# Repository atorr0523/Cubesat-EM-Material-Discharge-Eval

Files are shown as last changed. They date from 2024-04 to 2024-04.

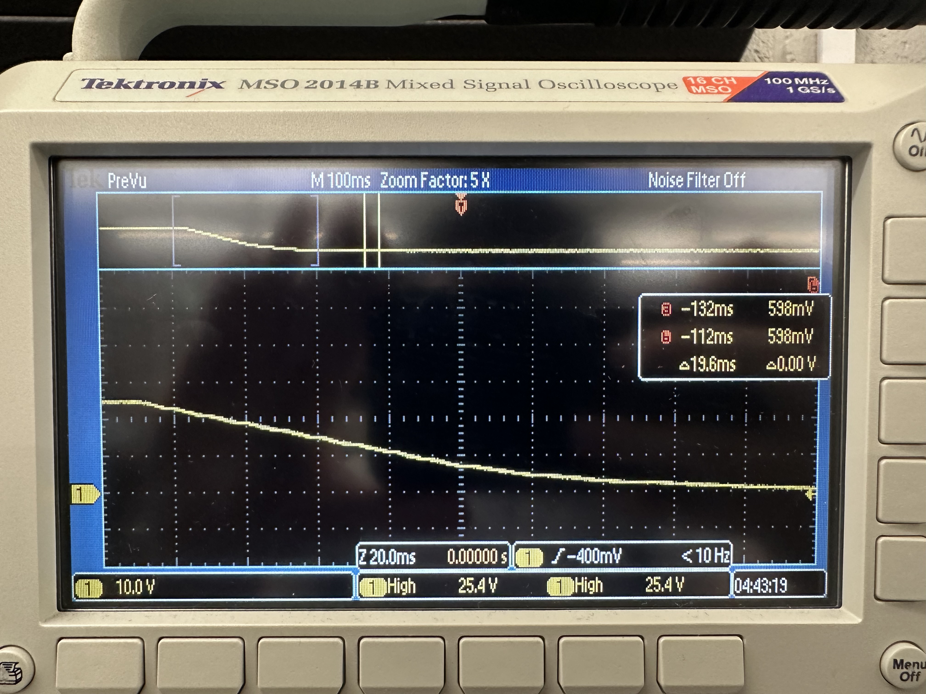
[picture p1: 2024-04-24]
ChassisandModeling/LVTesting/IMG_3064.jpg

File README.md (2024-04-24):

# CubeSat-EM-Material-Discharge-Eval
ECEN 403 904 Capstone Team 44 

For this project, we are tasked to design and develop the first prototype of Orbital Arc's RIOT Drive or CubeSat.

We divided it into 4 separate subsystems and at the end integrated each subsystem accordingly.

The Chassis and Modeling subsystem is designed to hold the integrated PCB as well as the accelerator plates that are designed.

The accelerator modeling subsystem helps with the design of the accelerator plate that would be mounted onto the CubeSat.
Simulations were performed amongst 3 different geometries and 3 different materials in order to see which iteration of 
the plate would fit well within the CubeSat's standards. 

The microcontroller subsystem, which is powered from the power PCB, helps control the system as well as the stepper motor controller which is used
for a gas feed valve.

The power circuit subsystem takes the input voltage and converts the voltage to power the components within the system.

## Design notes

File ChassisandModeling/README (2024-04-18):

My Chassis and Modeling folder contains the work performed for creation of the Chassis and Mounting, as well as other tasks completed by me

In this Chassis Files Folder, one will find the Solidworks and .stl files for the componenets created for this project.
In the LVTesting Folder, one will find the results from the low voltage testing performed at the beginning of the Spring 24 semester.
In the MISC. Folder, one will find hand-drawn engineering drawings or calculations in order to provide a path to continuation for interested parties.

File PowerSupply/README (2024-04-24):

For the Power Supply subsystem you will find the altium files before integrating with the microcontroller. 

The final design included the following:
  -A boost converter which steps up the voltage from 24V to 48V with a 0.62A output current needed.
  -A buck converter which steps down the voltage from 24V to 5V with a maximum output current of 2A needed for the thermionic cathodes.
  -A buck converter which steps down the voltage from 24V to 5V with a maximum output current of 1A needed for the stepper motor controller
  -A buck converter which steps down the voltage from 24V to 3.3V with a maximum output current of 1A needed to power the microcontroller.

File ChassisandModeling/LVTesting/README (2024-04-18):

This folder holds the data collected and Oscilloscope screenshots from the low voltage testing performed for Orbital Arc.
This testing was performed in order to provide Orbital Arc preliminary data of how the voltage applied to the accelerator plate will dissipate and how often it will need to be pulsed
The conclusion of this testing was that the dissipation over the intended operating range (First 10% of discharge) would be linear, and further high voltage testing would be required to get the actual dissipation curve
At this point, further testing was not able to take place and neglected, with my priority shifting to physical integration of the prototype

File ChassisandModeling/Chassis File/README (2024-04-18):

This folder contains all of the design files for the Chassis and Mounting Devices created. 
It also contains the files for the connector to the gas feed valve and DC Motor
This folder contains Solidworks files, Solidworks drawings, and .STL files

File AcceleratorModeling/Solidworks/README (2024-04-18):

These files are created in the Solidworks software. They are created for the nine geometry-material prototypes and to be tested with. There is another file for the chosen prototype with designed mounting. 
The Circular Plates are fabricated by hand so there are no Solidworks files for them.

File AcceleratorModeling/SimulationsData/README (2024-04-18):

These are files that contain the simulations from the ANSYS Maxwell software. These are created to simulate the electric field for each prototype after charging with 100kV. There is also an spreadsheet that contains the data that I have collected.

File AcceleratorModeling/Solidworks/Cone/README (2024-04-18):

These are files for the cone-shaped prototypes

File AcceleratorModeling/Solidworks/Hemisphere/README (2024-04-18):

These are files for the hemisphere-shaped prototypes

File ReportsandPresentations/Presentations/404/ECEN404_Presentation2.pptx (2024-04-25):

## ECEN 404 Team #44 Biweekly Update 2 Cubesat EM Material Discharge Eval: Ian Poynter Joshua Feldman Michael Kim Alejandro Torres Sponsor: Orbital Arc & SATOP TA: Souryendu Das

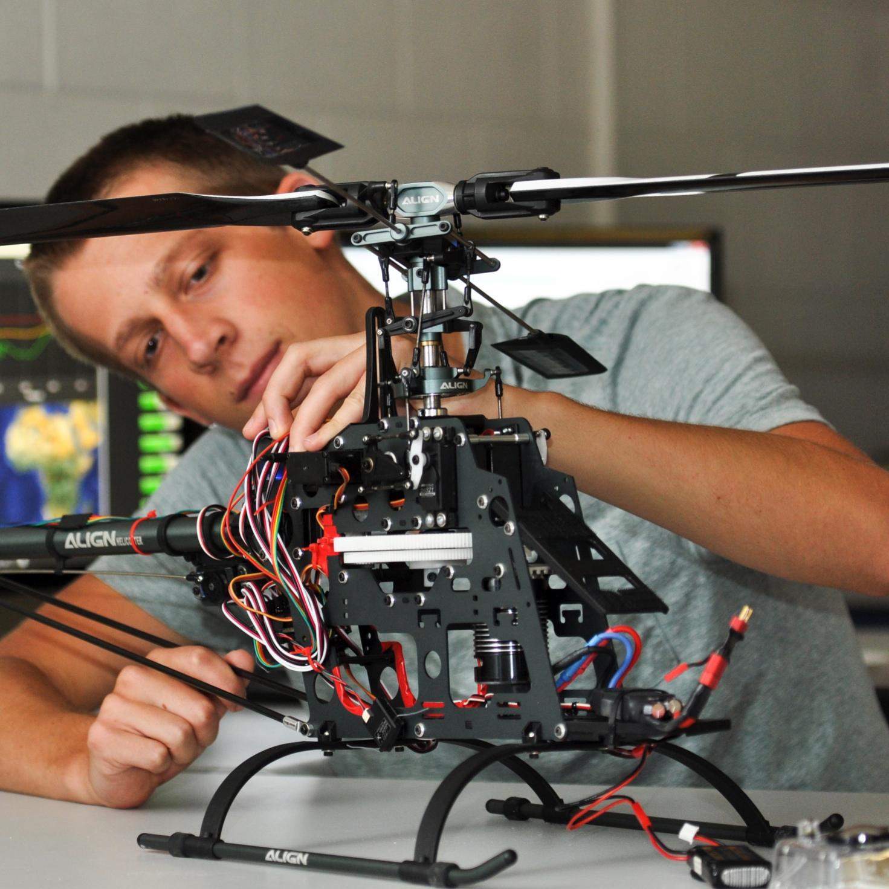
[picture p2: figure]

## Project Summary

- Develop the first prototype for the RIOT Drive
  - Interior Electronics
  - Gas Feed Control
  - Component Selection for Accelerator Plate

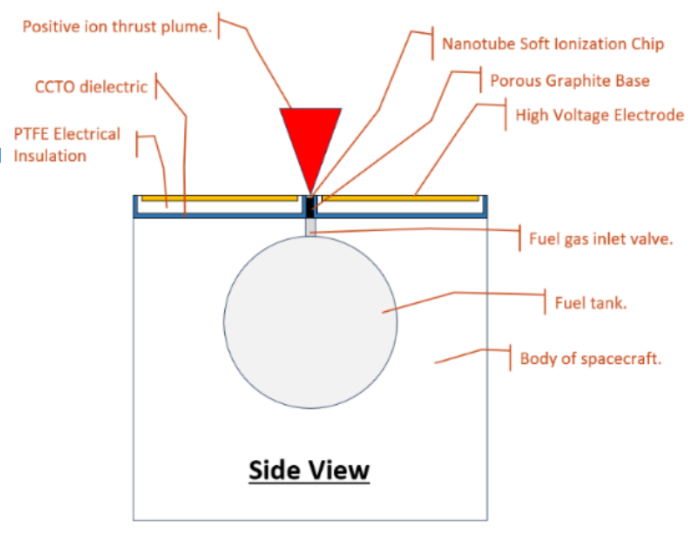
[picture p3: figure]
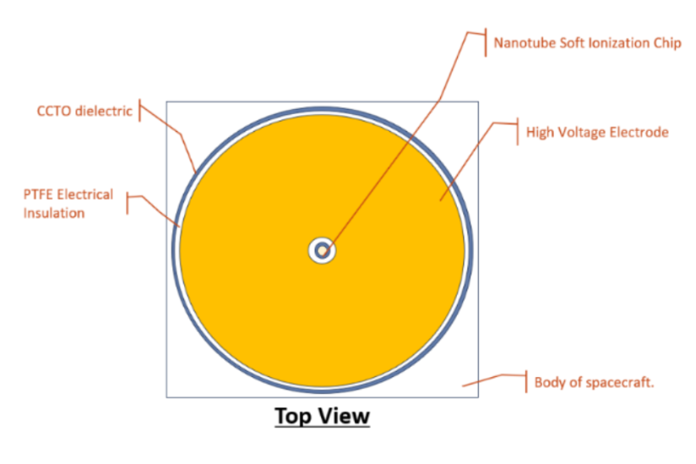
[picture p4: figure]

## Diagram of Subsystems

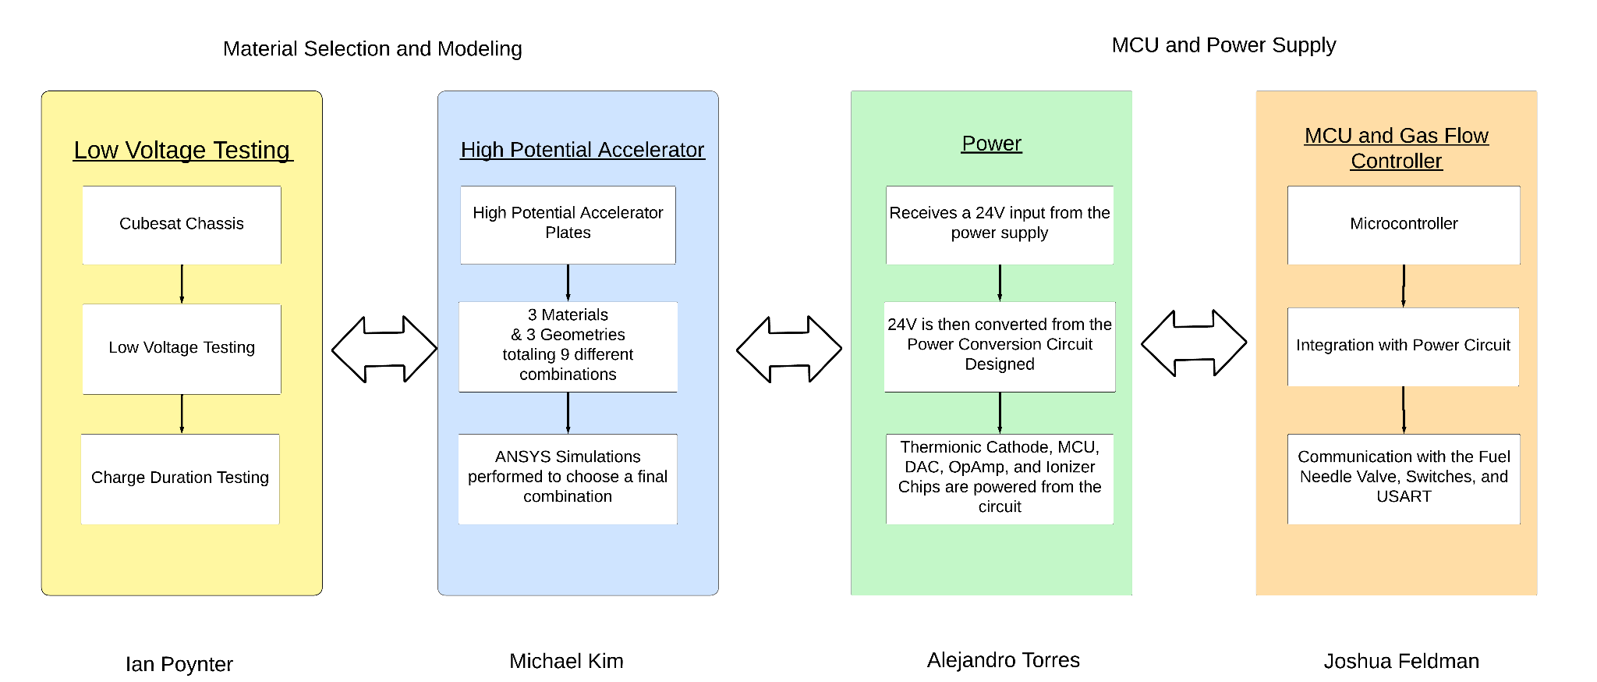
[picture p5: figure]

## Project Timeline

Mechanical Subsystems Design and Testing (completed 12/3) | Hardware Subsystems Redesign and Testing (to complete by 2/22) | Integration of Microcontroller and Power Subsystems (to complete by 3/18) | Validation of Integrated Hardware (to complete by 3/28) | Component Selection for Accelerator Plate (to complete by 3/28) | Final Integration (to complete by 4/12) | Final Demo (to complete by 4/19)

## Power Subsystem Alejandro Torres

Accomplishments since Presentation 1 18 hrs of effort | Ongoing progress/problems and plans until the next presentation
Completed Altium Schematic and PCB Layout configured and routed for integration with Microcontroller PCB and parts ordered to test in preparation for integration | Solder PCB and test through E-Load in preparation for integration with Microcontroller

## Microcontroller Joshua Feldman

Accomplishments since Presentation 1 20 hrs of effort | Ongoing progress/problems and plans until the next presentation
Reworked microcontroller board for changed inputs, for easier programming, and for future integration with power PCB. Ordered parts for PCB. MCU coded and tested for sending user inputs and control bits to DAC through SPI. | Order Fuel Valve Rework and order PCB for stepper motor control. Continue working with Alejandro for PCB integration.

## Low Voltage Physical Testing Ian Poynter

Accomplishments since Presentation 1 18 hrs of effort | Ongoing progress/problems and plans until the next presentation
Developed low voltage test setup and procedure Ordered parts for testing | Construct testing setup on breadboard Perform trial tests and validate data with sponsor

## High Potential Accelerator Plate Michael Kim

Accomplishments since Presentation 1 16 hrs of effort | Ongoing progress/problems and plans until the next presentation
Completed high-voltage simulations of circular plate geometry on Ansys Maxwell software. | Complete high-voltage simulations for hemisphere geometry. Start high-voltage simulations for cone geometry.

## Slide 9

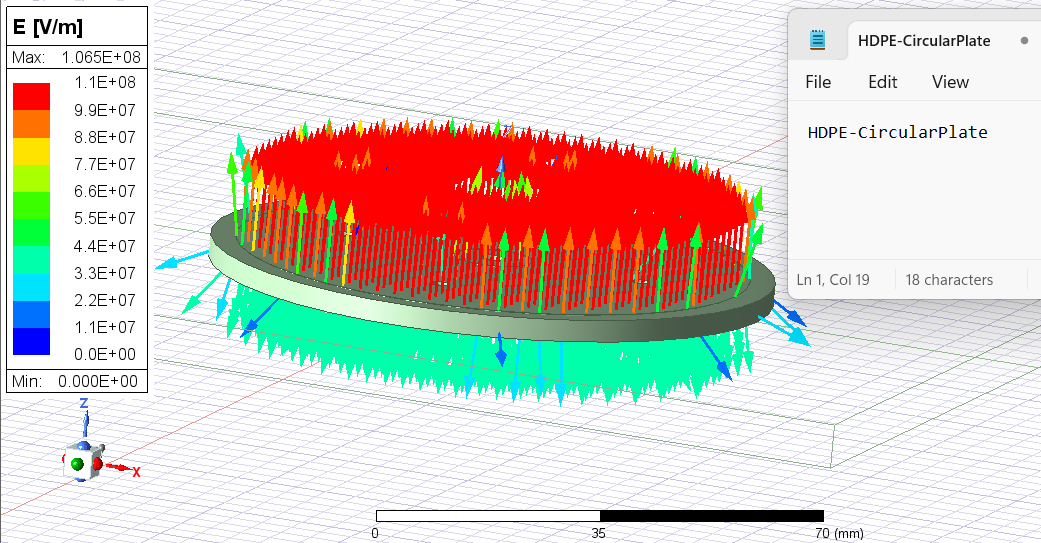
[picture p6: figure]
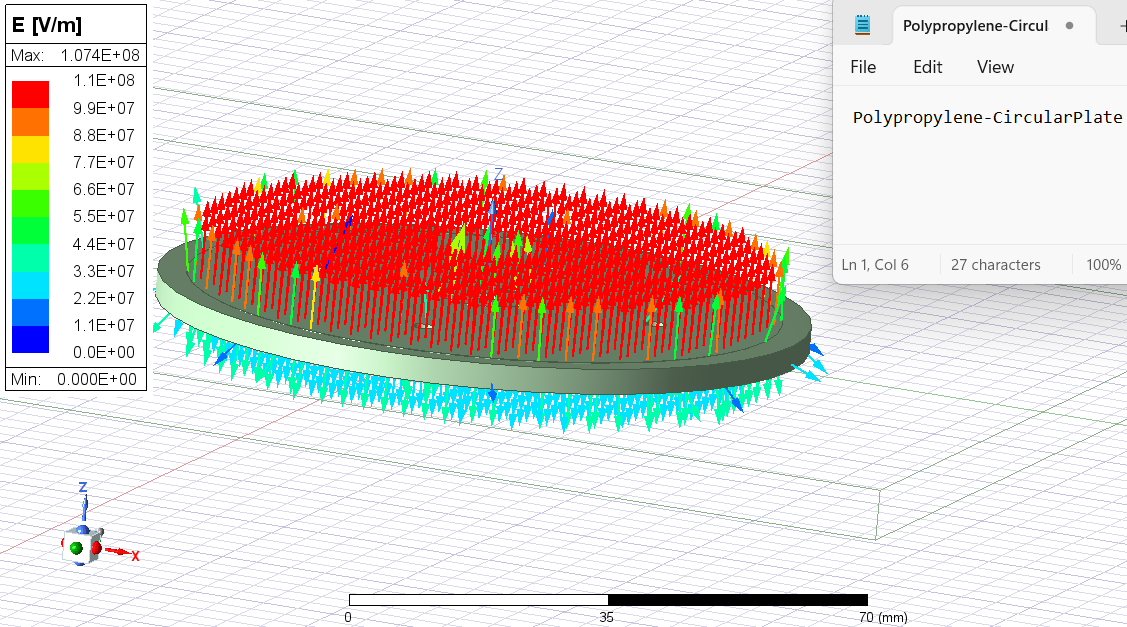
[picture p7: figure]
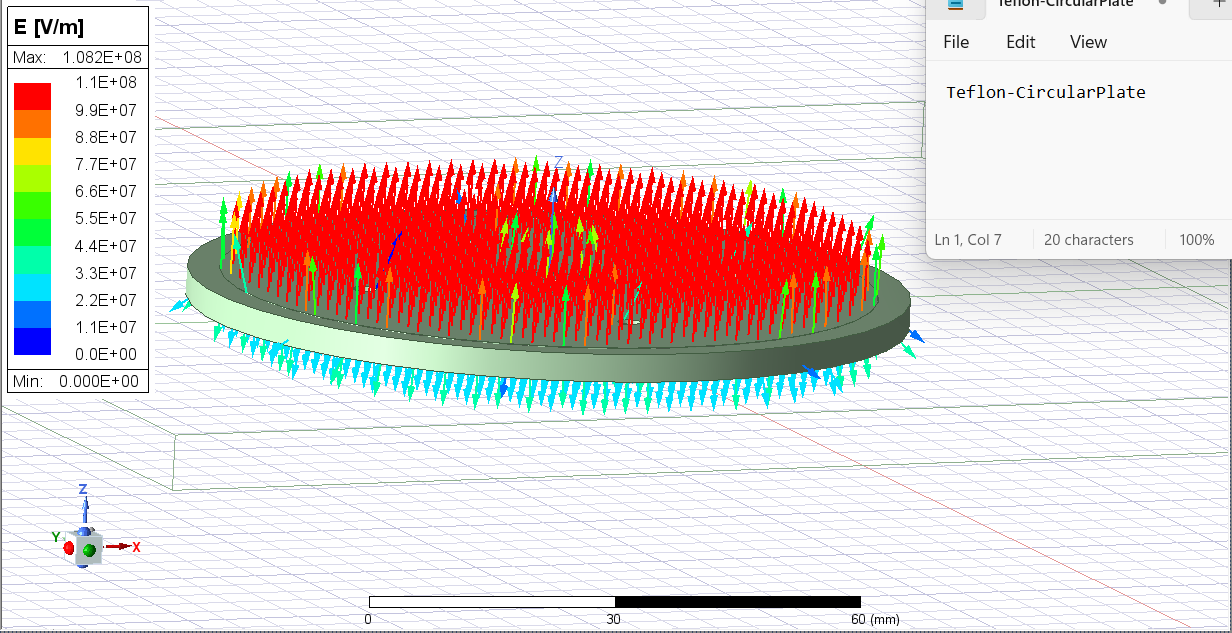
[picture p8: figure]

## Execution Plan

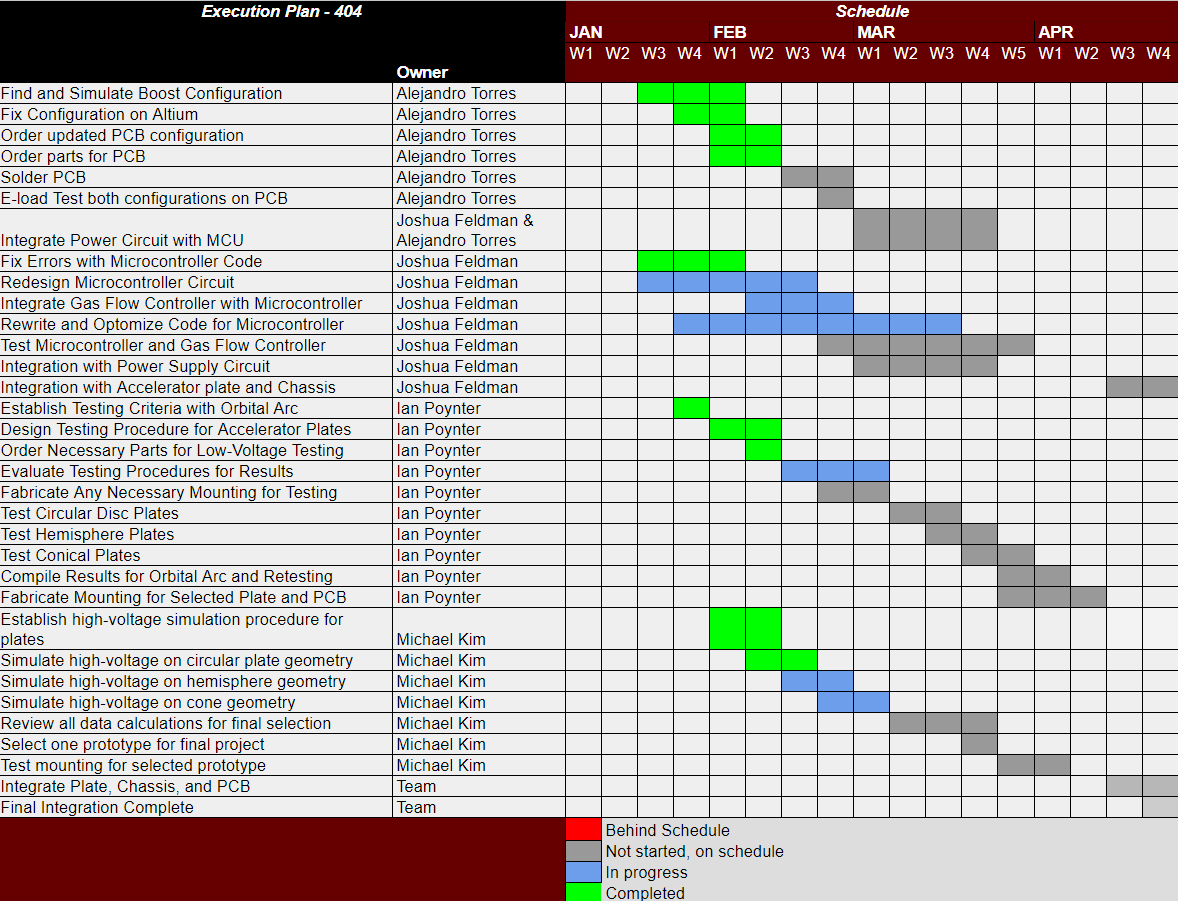
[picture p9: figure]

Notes: Michelle

## Validation Plan

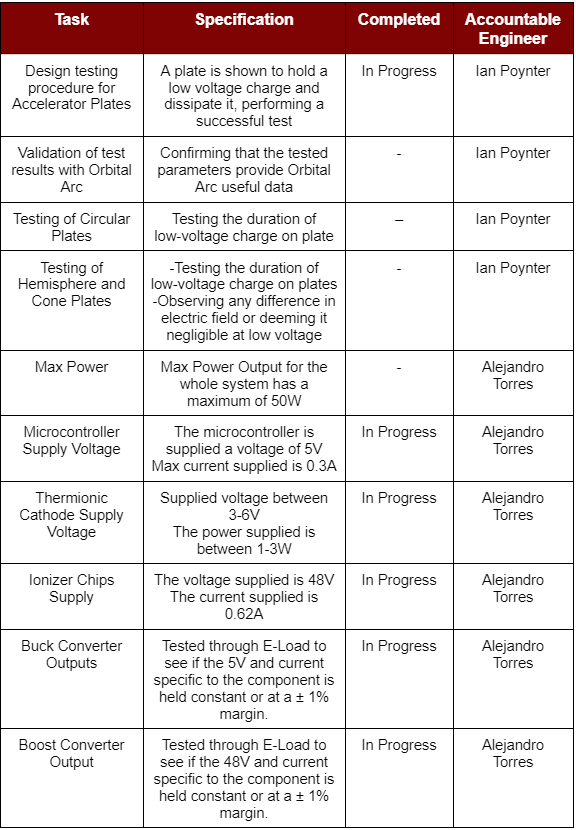
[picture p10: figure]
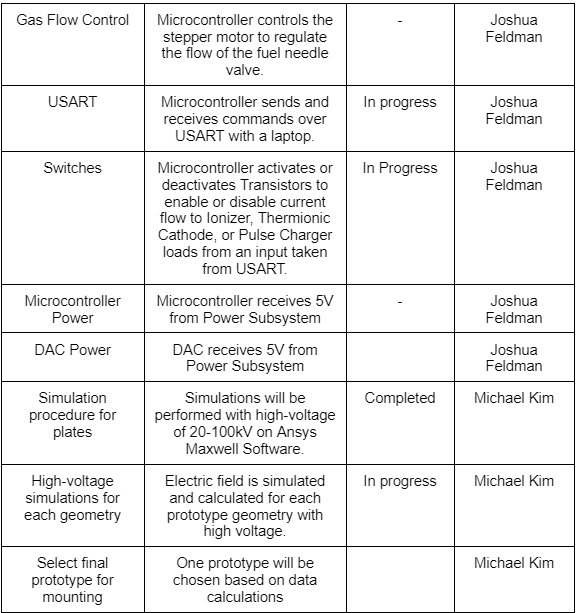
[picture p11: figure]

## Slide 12

Thank you!

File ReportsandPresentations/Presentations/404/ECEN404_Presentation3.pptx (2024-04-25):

## ECEN 404 Team #44 Biweekly Update 3 Cubesat EM Material Discharge Eval: Ian Poynter Joshua Feldman Michael Kim Alejandro Torres Sponsor: Orbital Arc & SATOP TA: Souryendu Das

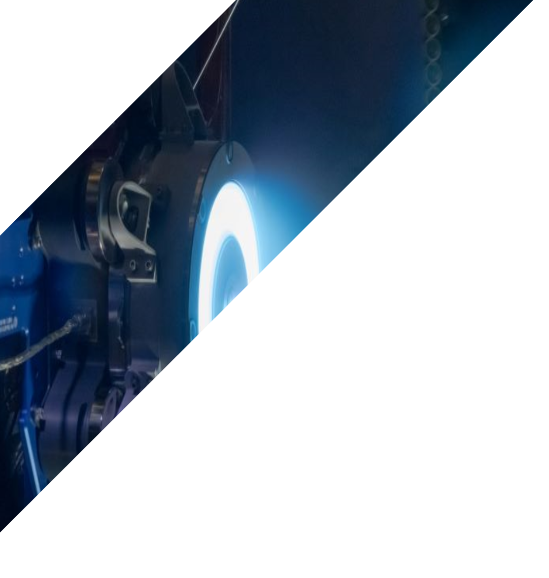
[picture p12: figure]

## Problem Statement

Current Ion Thrusters have limited use cases due to many factors, including fuel cost and harsh ionization methods

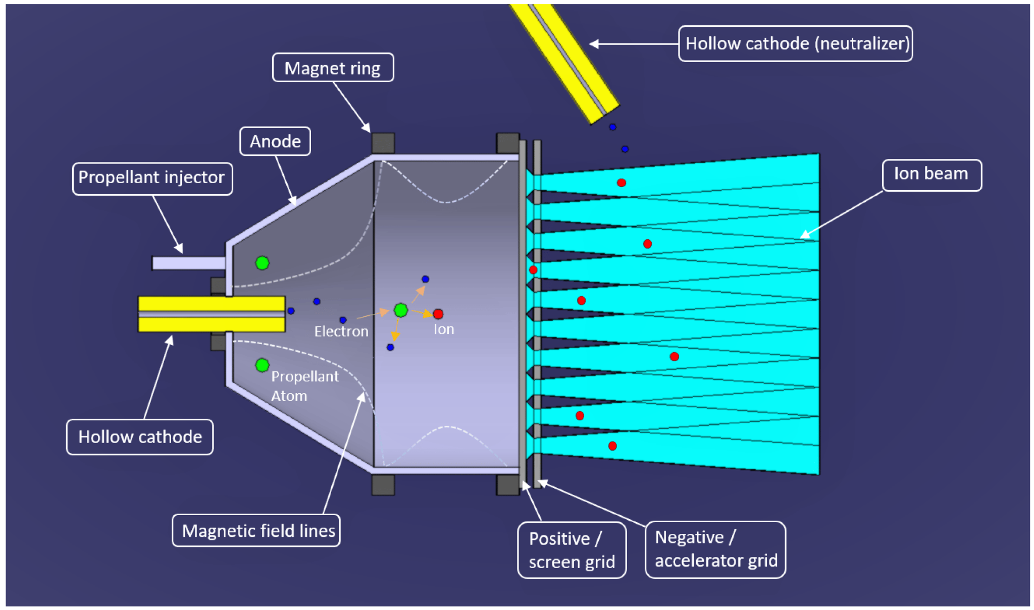
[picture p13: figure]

## Project Summary

RIOT Drive: New type of Ion Thruster that will reduce these limitations and operate with higher efficiency
Solution
- Develop a prototype for the RIOT Drive
  - Internal Hardware
    - Power Supply
    - Microcontroller
  - Accelerator Plate
    - Geometry Selection


## Diagram of Subsystems


## Project Timeline

Mechanical Subsystems Design and Testing (completed 12/3) | Hardware Subsystems Redesign and Testing (to complete by 2/22) | Integration of Microcontroller and Power Subsystems (to complete by 3/18) | Validation of Integrated Hardware (to complete by 3/28) | Component Selection for Accelerator Plate (to complete by 3/28) | Final Integration (to complete by 4/12) | Final Demo (to complete by 4/19)

## Power Subsystem Alejandro Torres

Accomplishments since last update 16 hrs of effort | Ongoing progress/problems and plans until the next presentation
Boost Converter soldered and E-load tested. | Fix Boost Converter maximum load current. Solder and test the rest of the PCB. Configure Altium Schematic for Buck converter to power the stepper motor drive.

## Power Subsystem Alejandro Torres

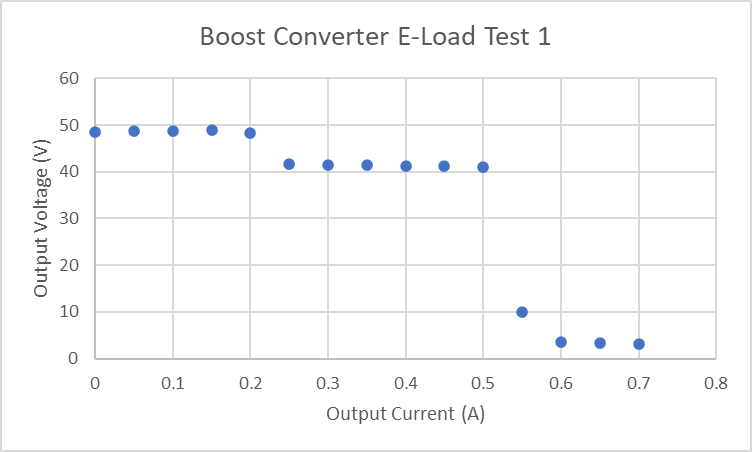
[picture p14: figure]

- Boost Converter Tested through Electronic Load.
- 48V was not kept constant throughout varying load currents in Test 1 and Test 2.
- Need to configure PCB to fix this issue.

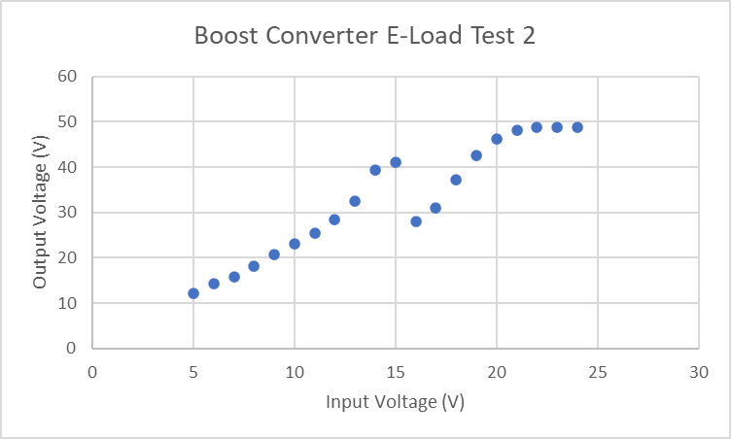
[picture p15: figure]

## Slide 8

Microcontroller
Joshua Feldman

Accomplishments since last update 12 hours of effort | Ongoing progress/problems and plans until the next presentation
Re-coded microcontroller for sponsor’s change to gas flow valve and stepper motor. Changed PCB to send inputs to stepper motor driver and removed now obsolete parts. Ordered board and parts for new revision. | Solder PCB after presentation. Test board with Stepper motor driver, and add stepper motor driver to PCB. Test powering microcontroller with Alejandro’s power PCB after testing board in lab and during Blitz.

## Low Voltage Physical Testing Ian Poynter

Accomplishments since last update 10 hrs of effort | Ongoing progress/problems and plans until the next presentation
Performed initial low-voltage discharge testing Reviewed data with sponsor | Work with Michael to make accelerator plate selection Begin mounting design

## High Potential Accelerator Plate Michael Kim

Accomplishments since last update 20 hrs of effort | Ongoing progress/problems and plans until the next presentation
Completed simulations for hemisphere and cone geometries. | Compare simulations using Gauss’s Law Work with Ian to select final prototype based on reviewed data.

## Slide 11

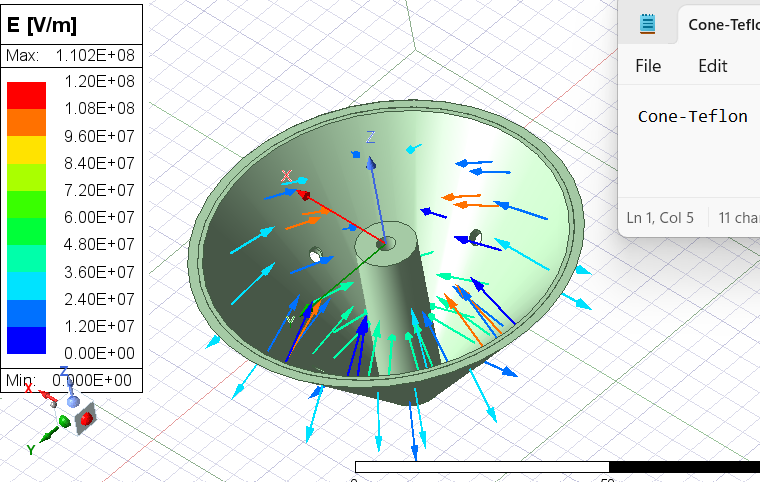
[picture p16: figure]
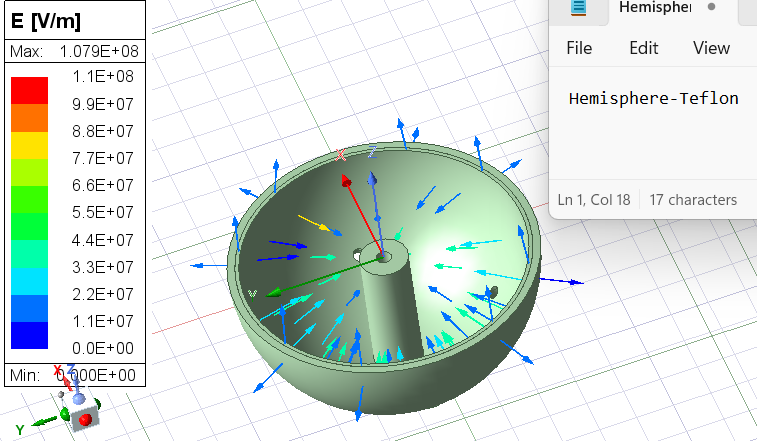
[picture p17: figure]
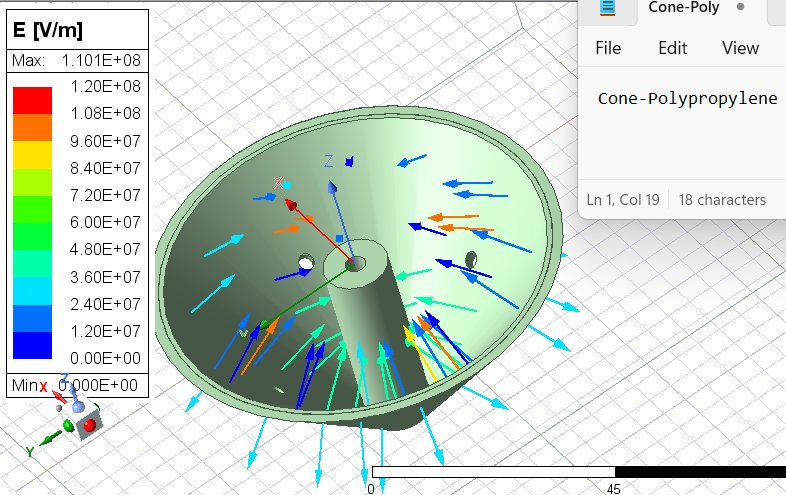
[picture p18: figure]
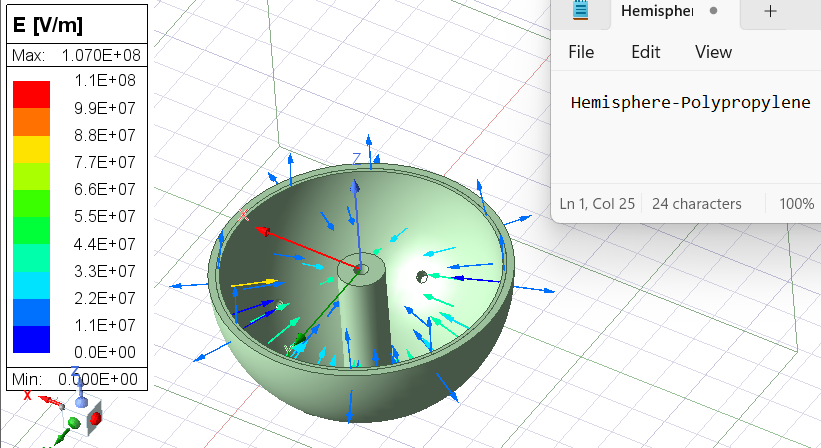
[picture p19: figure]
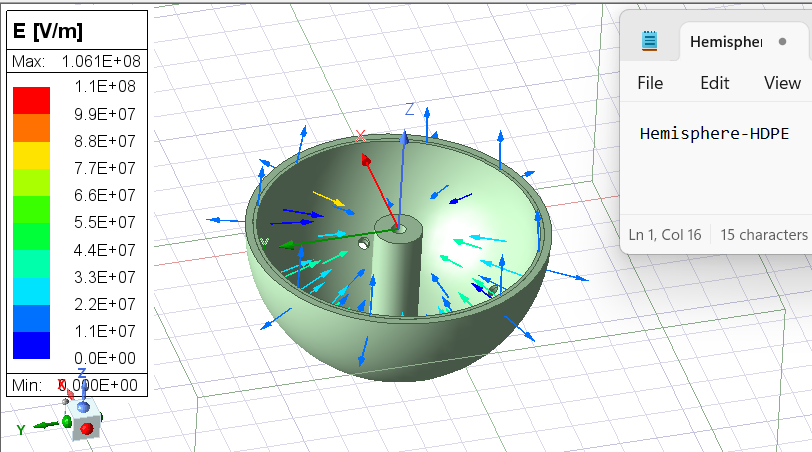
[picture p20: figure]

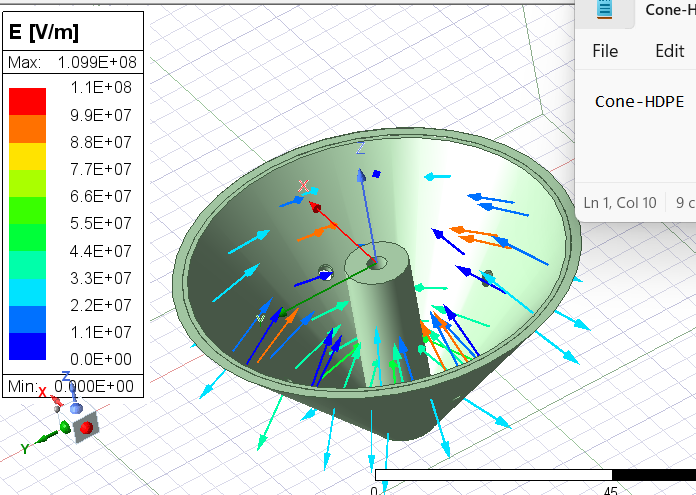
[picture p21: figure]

## Execution Plan

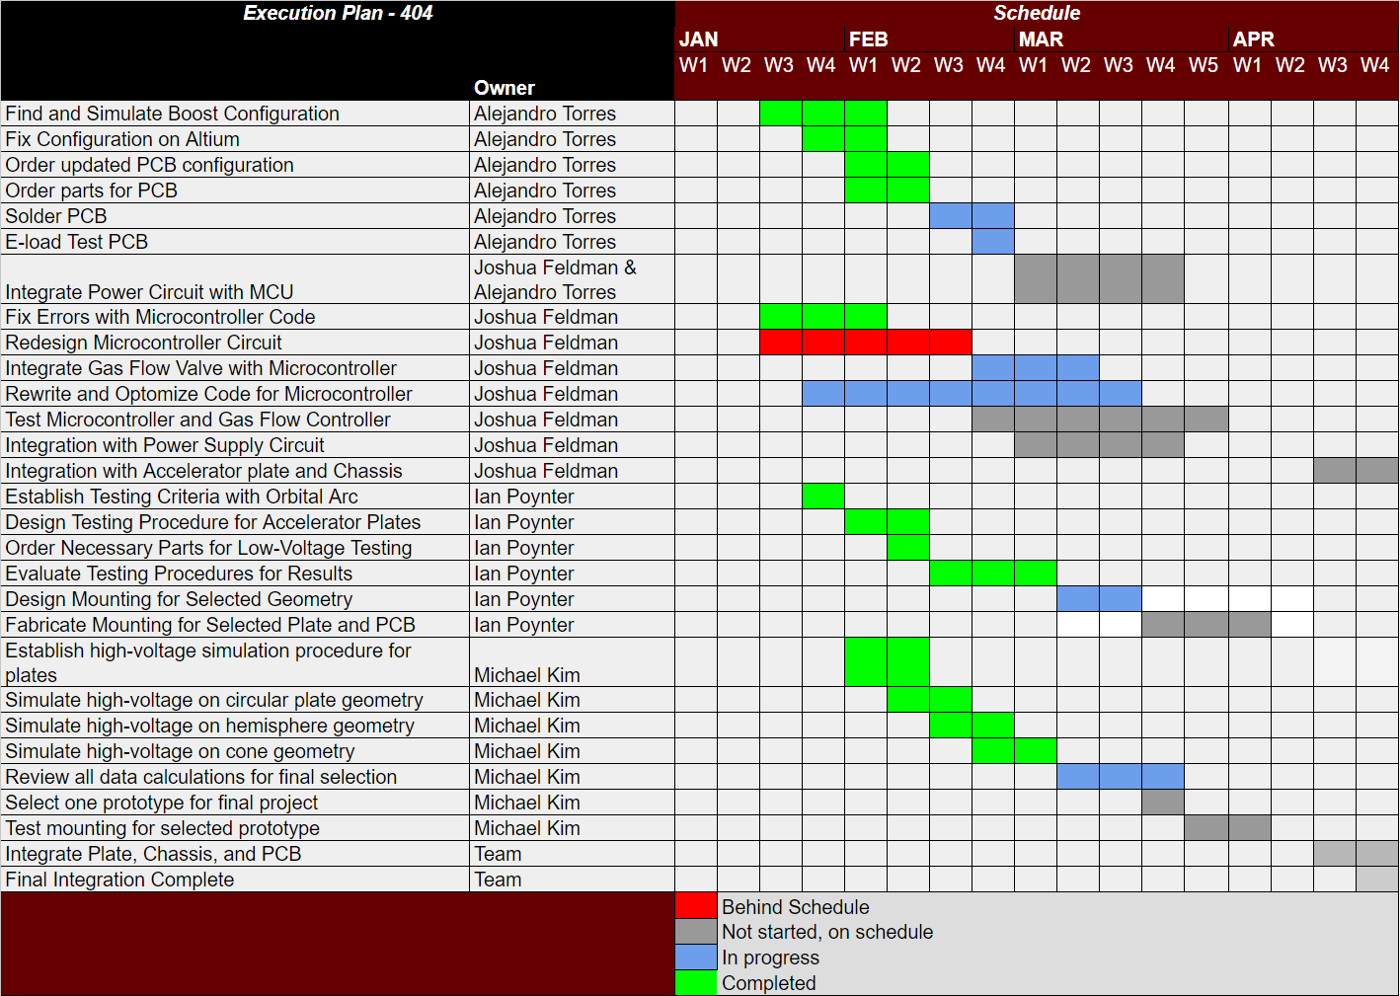
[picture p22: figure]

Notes: Michelle

## Validation Plan

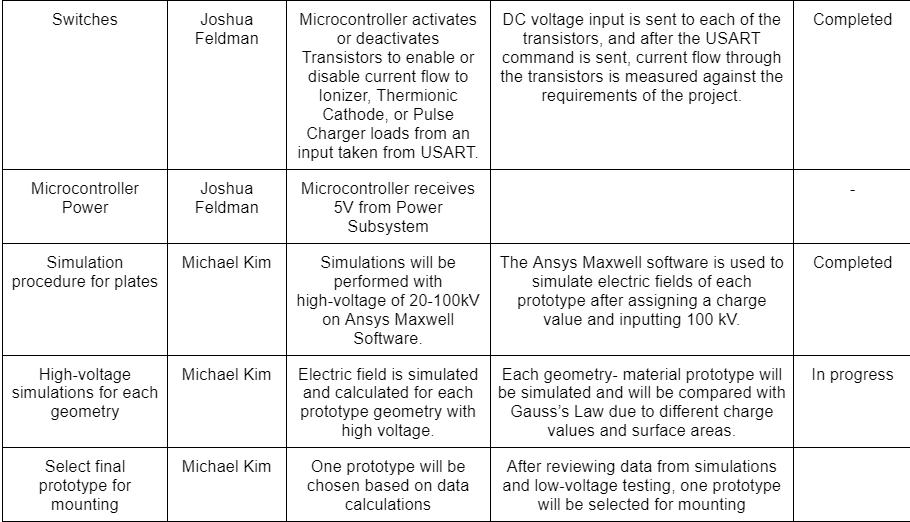
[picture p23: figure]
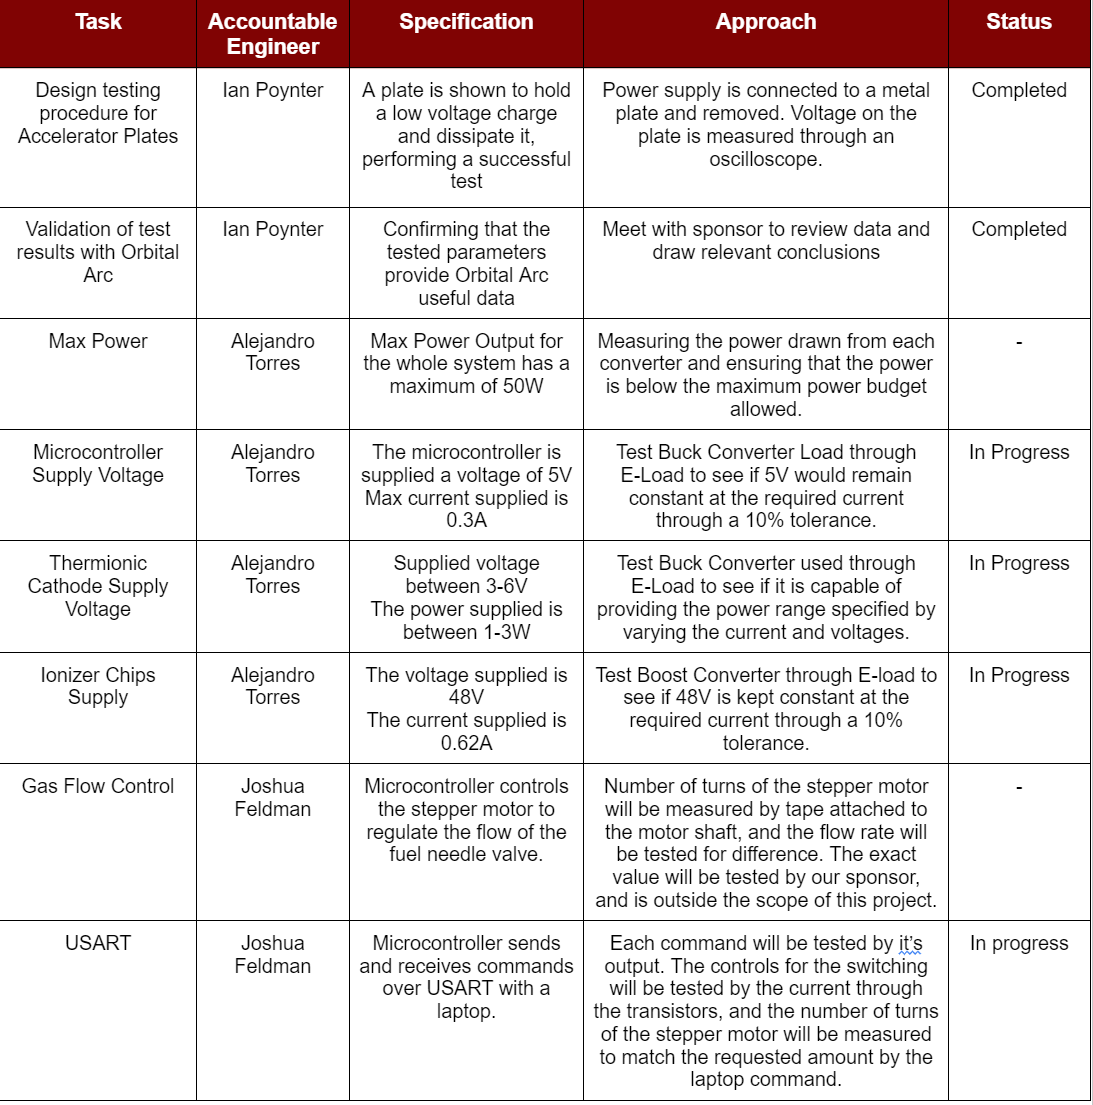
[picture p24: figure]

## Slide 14

Thank you!

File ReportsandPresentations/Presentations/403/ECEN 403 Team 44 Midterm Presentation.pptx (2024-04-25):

## ECEN 403 Team #44 Cubesat EM Material Discharge Eval: Joshua Feldman Michael Kim Ian Poynter Alejandro Torres Sponsor: Orbital Arc & SATOP TA: Peng-Hao Huang


## Current Ion Thrusters

- Current ion thrusters require expensive fuel, have extremely low acceleration, and require electron bombardment for ionization.


## RIOT Drive


- Develop a prototype for the RIOT Drive, an ion thruster that can use cheaper fuel and will operate at about 4 times the efficiency of contemporary ones.


## Diagram of Subsystems and Interface

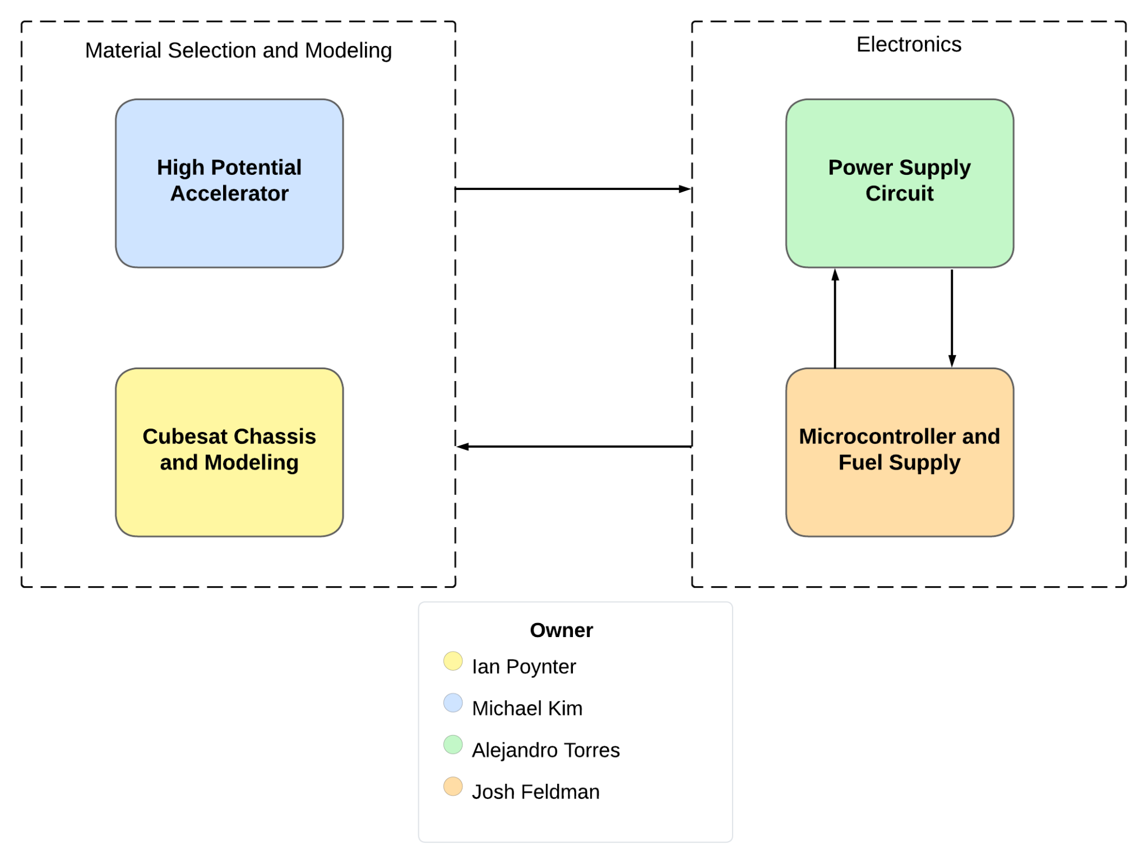
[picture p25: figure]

## Task Partition

- Michael: Accelerator Plate & Shielding
- Josh: Microcontroller and Fuel Supply
- Alejandro: Power Supply Circuit
- Ian: CubeSat Chassis and Modeling

## Accelerator Plate and Shielding

-Materials and geometries are tested for one combination for final project.
-Materials are specifically chosen to be space launch ready.
-Geometries are designed for electric field optimization.
-Internal components are shielded from voltage of the accelerator.

Geometries | Materials
Circular Plane | Copper
Hemisphere | Aluminum
Parabolic Pyramid | Titanium

## Microcontroller

- Will regulate fuel flow to ionizer chips.
- Will time the pulse charger for the accelerator plate.
- Enables the accelerator, ionizer, and thermionic cathode.

## Fuel Supply

- Gas fuel line will be composed of PTFE tubing
- Fuel valve will interface with microcontroller to regulate fuel delivery
- Multiple tubing sizes will be tested


## Power Supply Circuit

- 50W power budget
- 24V Input
- Outputs
  - High Voltage Accelerator
    - Needs 3-6V to be boosted to 100 kV using a Pulse Generator
  - Thermionic Cathode
    - 3-6V
  - Ionizer Chips
    - 33V
  - Microcontroller
    - 3.3V
  - DAC
    - 3V
  - Gas Feed Control


## Power Supply Circuit Breakdown


## CubeSat Chassis and Modeling

- Footprint of prototype must fit within 1U CubeSat
- Mounting locations for subsystems
- Responsible for risk calculations


## Limitations

- Ionizer chips will not be provided for the prototype
- Must fit within one unit of a CubeSat
- Restrictive specifications for multiple components
- Sponsor may request that additional materials be tested

## Execution Plan


## Validation Plan


## Questions?

## Thank You

## References

- https://orbitalarc.com/
- https://www.mdpi.com/2076-3417/13/9/5600
- https://www.aliexpress.us/item/3256805375098239.html?gatewayAdapt=glo2usa4itemAdapt

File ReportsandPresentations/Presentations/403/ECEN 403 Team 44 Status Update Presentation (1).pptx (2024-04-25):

## ECEN 403 Team #44 Cubesat EM Material Discharge Eval: Joshua Feldman Michael Kim Ian Poynter Alejandro Torres Sponsor: Orbital Arc & SATOP TA: Peng-Hao Huang


## RIOT Drive


- Construction of the first prototype for the RIOT Drive by Orbital Arc
  - Accelerator Plate Data
  - Microcontroller System
  - Power Supply Circuitry
  - Chassis Design


## Diagram of Subsystems and Interface


## System Block Diagram


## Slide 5

CubeSat Chassis Ian Poynter

Accomplishments since the last presentation | Ongoing progress/problems and plans until the next presentation
-Capstone team made decision to build instead of buy -Aluminum stock for parts ordered -Engineering drawings for part outlines | -Create chassis/parts using CAD software -Begin fabrication of corner pieces for chassis

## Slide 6

High Potential Accelerator Plate Michael Kim

Accomplishments since the last presentation <~48> hrs | Ongoing progress/problems and plans until the next presentation
Finalized the designs of all 3 geometries using Blender. Ordered parts, including the materials needed for fabrication. Confirmed type of material with our sponsor. | Craft the circular plate. Begin fabricating the Hemisphere Geometry.

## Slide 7


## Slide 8

Power Supply Circuit Alejandro Torres

Accomplishments since the last presentation <~90> hrs | Ongoing progress/problems and plans until the next presentation
Simulated Buck Converter on LTSpice Simulated Boost Converter on WEBENCH Ordered Parts needed for PCB Design Finished PCB Design to power external components | Testing Pulse Generator that was given to us by our sponsor Solder, test, and debug PCB

## Schematics and Simulations


## Design


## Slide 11

Microcontroller Joshua Feldman

Accomplishments since the last presentation <~45> hrs | Ongoing progress/problems and plans until the next presentation
Additional components for PCB researched. Reviewing specs and datasheets for parts. Schematic for PCB created in Altium. Symbols and Footprints of all parts in Altium. Switches simulated in Mulitsim to ensure they function with the input voltages and currents. | PCB interfaces with Power subsystem, so placement of components may need to be changed for subsystem integration. Microcontroller programming and testing PCB.

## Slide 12


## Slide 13


## Execution Plan


## Validation Plan


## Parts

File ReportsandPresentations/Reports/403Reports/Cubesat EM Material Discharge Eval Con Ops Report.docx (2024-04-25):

Cubesat EM Material Discharge Eval

Joshua Feldman

Michael Kim

Ian Poynter

Alejandro Torres

Concept of Operations

REVISION – Draft

9/14/2023

Concept of Operations

for

Cubesat EM Material Discharge Eval

Team 44

Approved by:

_____________________________

Project Leader Date

_____________________________

Prof. Kalafatis Date

_____________________________

T/A Date

Change Record

Rev. | Date | Originator | Approvals | Description
- | [9/14/2023] | [Ian Poynter] | | Draft Release
1 | [12/3/2023] | [Ian Poynter] | | End of Semester Revision

Table of Contents

Table of Contents 3

1. Executive Summary 4

2. Introduction 5

2.1. Background 5

2.2. Overview 6

2.3. Referenced Documents and Standards 6

3. Operating Concept 7

3.1. Scope 7

3.2. Operational Description and Constraints 7

3.3. System Description 7

3.4. Modes of Operations 8

3.5. Users 8

3.6. Support 8

4. Scenario(s) 9

4.1. Orbiting Satellites 9

4.2. Deep Space Propulsion 9

5. Analysis 10

5.1. Summary of Proposed Improvements 10

5.2. Disadvantages and Limitations 10

5.3. Alternatives 10

5.4. Impact 10

# 1. Executive Summary

As humanity continues to prioritize space travel, new technologies continue to be developed that help sustainable interplanetary travel become a reality. Ion thrusters are one such technology, creating thrust by accelerating ions with a high voltage. The ion thruster was first proposed in 1911 and first built successfully in 1959 at NASA, but current ion thrusters have low acceleration and require expensive Xenon as fuel. The Relativistic Ion Thrust Drive, or RIOT Drive, proposed by Orbital Arc plans to change that. The RIOT Drive will use a gentler ionization method than current Hall-Effect or gridded thrusters so cheaper and heavier fuel can be used, providing a much stronger propulsion and higher efficiency. For this project, we will design the chassis and essential systems of the first working prototype of the RIOT Drive, to produce a proof of concept that is functional enough to entice investors to sponsor a larger-scale project.

# 2. Introduction

The Relativistic Ion Thrust Drive, or RIOT Drive, is an ion thruster that will ionize the fuel more gently than contemporary thrusters. This will allow the RIOT drive to use heavier fuel and accelerate the ions at a higher velocity providing about four times more efficiency than current ion thrusters. We will design the geometry, chassis, and software for a prototype of the RIOT Drive for Orbital Arc to improve in the future. Deliverables will include a CubeSat Standard compliant chassis, a functional power supply circuitry and microcontroller system for testing, and data collection coming from electrostatic potential testing on different accelerator plate shapes and insulating materials.

## 2.1. Background

Ion thrusters are used for deep space travel in a variety of applications: from adjusting satellite orbits to propelling spacecraft throughout the solar system [1]. The most common types of ion thrusters are electrostatic or gridded, and electromagnetic or Hall-effect thrusters. Gridded Ion thrusters are more commonly used [2], and they operate by adding electrons to fuel to produce ions [1] and then accelerating the ions at a high velocity through electrically charged grids at the back of the thruster to produce thrust [2]. Most ion thrusters ionize by bombarding the atoms with high-energy electrons producing a positively charged ion [1]. The most common propellant used in ion thrusters is Xenon because it is easily ionized, it has high atomic mass, and it is a noble gas. These properties allow the ion thruster to have higher efficiency than less easily ionizable atoms, generate stronger thrust than other lighter ions, and remain stable during the ionization process. [1] [2].

The primary parts of an ion propulsion system include the ion thruster, the power processing unit, the propellant management system, and the digital control interface unit [1]. To power an ion thruster, electricity is provided by a spacecraft’s solar panels, [2] then the power processing unit, or PPU, converts the electricity into the voltages needed to accelerate the ions [1].

Orbital Arc was founded in February 2023 from the idea of the Relativistic Ion Thrust Drive or RIOT Drive. The RIOT drive is based on a linear particle accelerator and ionization without bombardment. With a linear particle accelerator, the exhaust velocity will reach several percent of the speed of light and exhibit relativistic mass expansion. These factors will increase the efficiency of the RIOT Drive over contemporary ion thrusters by about 4 times [3]. The second component of the RIOT Drive is the method of ionization. The current bombardment method of ionization will break molecular bonds, so an atomic fuel like Xenon must be used. The ionization of the RIOT Drive will use field effect ionization to generate ions cold and accelerate them without containment. This eliminates the problems of bombardment and allows a heavier fuel such as Sulfur Hexafluoride to be used [3].

## 2.2. Overview

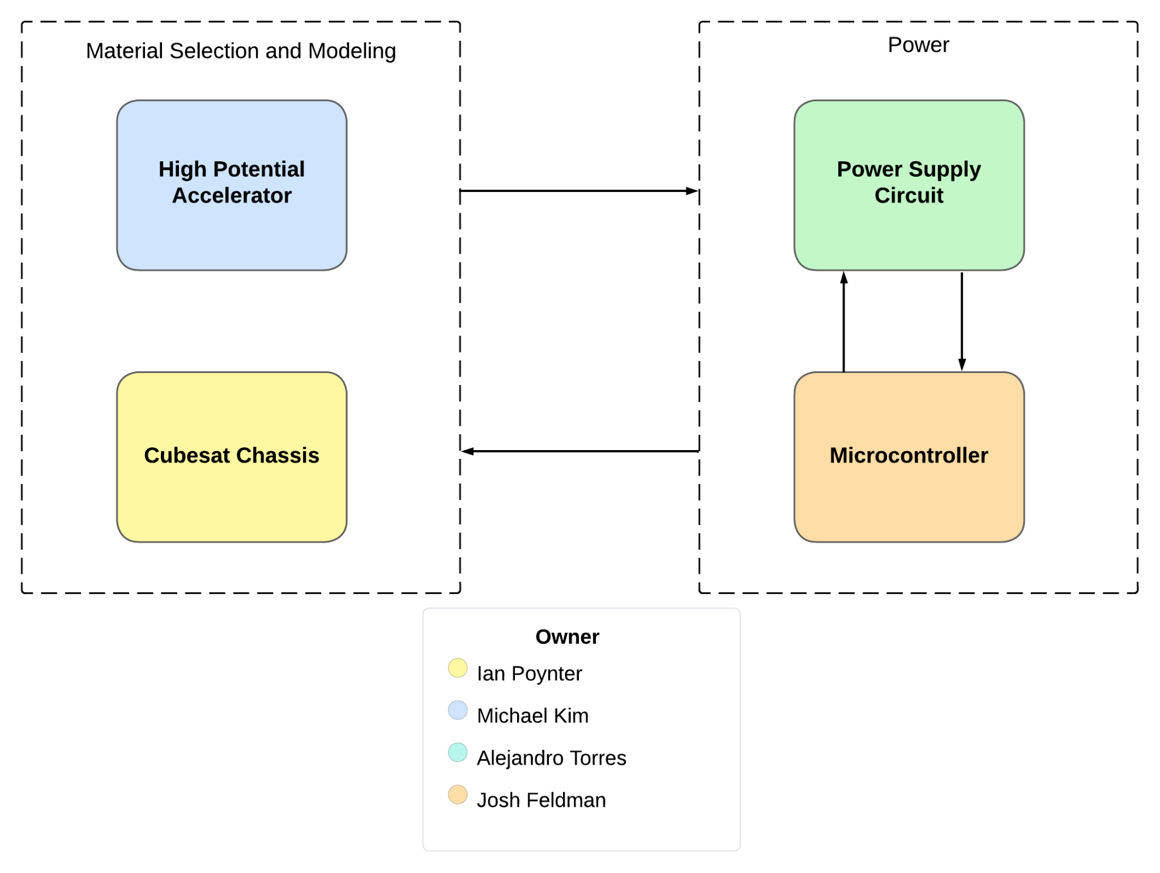
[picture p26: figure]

The RIOT Drive is a type of electrostatic ion thruster designed for deep space travel and has the design capabilities that reduce its reliance on delta-v compared to current ion thrusters. The primary limiting factor on the application of the thrust will be the power system that the ion thruster employs. The system will be tested with three different materials and three different geometries, totaling 9 different prototypes to be modeled. The system will also implement a circuit design that will fit within one unit of a CubeSat and will adhere to the required design specifications to power the thruster.

## 2.3. Referenced Documents and Standards

1) Dunbar, Brian. “Ion Propulsion.” NASA, NASA, 18 Aug. 2015, www.nasa.gov/centers/glenn/about/fs21grc.html.
2) Wessels, Wessel. “Ion Thrusters - What They Are and How They Work.” Headed For Space, 30 Jan. 2023, headedforspace.com/ion-thrusters-and-ion-propulsion/
3) Orbital Arc, 16 Aug. 2023, orbitalarc.com/.

# 3. Operating Concept

## 3.1. Scope

The RIOT drive prototype will fit on a CubeSat and propel it into outer space using Sulfur Hexafluoride as fuel. The Sulfur Hexafluoride will be ionized by nanotechnology designed by Orbital Arc and accelerated by a high-voltage plate to provide thrust. The fuel will then be neutralized by electrons to prevent a positive charge buildup behind the thruster that reduces efficiency. This will make the thruster an efficient method of propulsion for space travel, and can potentially revolutionize deep space propulsion in the future. For our prototype, we will establish a power supply with the ability to reliably deliver the necessary power to all required components on board while operating in a space environment. Additionally, experimental data will be collected on different accelerator plate geometries and materials, as well as different shielding techniques.

## 3.2. Operational Description and Constraints

This project will be designed to function in the following conditions:

- Conditions of outer space, being a near vacuum environment and near absolute zero temperatures.
- The electronics need to be properly shielded from the normal operating voltage of 10kV and potential surges up to 100kV from the accelerator.
- The fuel supply needs to be precisely regulated over a large range of pressures.
- The solar panels that power the thruster need to receive enough sunlight as the CubeSat moves further from the sun.
- Many of the parts will be supplied by Orbital Arc, and will not be available for the demonstrations.

## 3.3. System Description

- Accelerator: A gridded accelerator allows ions to accelerate at high speed. It also uses relativistic mass expansion to vastly increase the effective mass of fuel flowing out of the thruster. Responsibilities include material and geometry selection, data collection, and construction of a final plate to integrate with the CubeSat
- Power Network: Responsible for delivering correct voltage and amperage to multiple components, including the high voltage accelerator plates, thermionic cathode, ionizer chips, gas feed control valves, etc. Will need to fit inside one CubeSat unit and be capable of regular function in a space environment.
- CubeSat Chassis and Modeling: Responsible for procurement and construction of the CubeSat prototype, as well as taking responsibility for design parameters around safety and ability to operate in space. Thermal considerations will need to be taken to keep the ambient temperature in the system at a temperature where all components can operate. Calculations will be done to ensure compliance with NASA’s outgassing and radiation standards where possible.
- Microcontroller: Where a fully functional RIOT Drive would utilize the on-board electronics of the spacecraft, our prototype will implement a microcontroller to control the electronics of the system. The microcontroller will be able to activate the pulse charger, thermionic cathode, and ionizer chip as needed. The microcontroller will be located on the same PCB as the power supply.

## 3.4. Modes of Operations

The RIOT drive will operate in normal propulsion mode and directional mode. Normal propulsion mode will accelerate the ions directly away from the CubeSat to propel it forward. The directional mode will induce a variable voltage on the plates to accelerate the ions at an angle. This can turn the CubeSat for any course corrections that are needed.

## 3.5. Users

The RIOT Drive prototype will be designed for use by Orbital Arc to provide them with testing data for future designs. The RIOT Drive has the potential to revolutionize space travel in the future and in the future will be an improvement over current ion thrusters in space missions for NASA, ESA, or any space exploration company.

## 3.6. Support

The users will be provided with support through instruction documents from Orbital Arc and meetings with Orbital Arc and the consumer company to discuss how the RIOT Drive will be used. For our prototype, thorough documentation of the design and operation will be provided through our FSR and ICD documents.

# 4. Scenario(s)

## 4.1. Orbiting Satellites

Ion thrusters play a pivotal role in the operation of orbiting satellites, from maintaining the orbit of China’s Tiangong Space Station to performing maneuvers for the SpaceX Starlink satellites. The efficiency of ion thrusters allows them to maneuver satellites in orbit with small amounts of fuel, allowing the satellites to operate for longer with a limited fuel source. Ion thrusters have great functionality in satellites, from small adjustments to deorbiting, and the RIOT Drive has the potential to accomplish these tasks more efficiently and cheaply.

## 4.2. Deep Space Propulsion

Ion thrusters are crucial propulsion systems for deep space missions. Although ion thrusters accelerate gradually, they offer unparalleled efficiency and longevity compared to traditional fuel-based propulsion. Ion thrusters have been instrumental in missions like NASA’s Dawn or the ESA’s BepiColombo, which are exploring the asteroid belt and Mercury, respectively. An ion thruster’s low fuel consumption and ability to operate over extended periods make them the best choice for enabling intricate trajectories and exploration beyond the Earth’s orbit. The superior fuel efficiency and cost of the RIOT Drive compared to contemporary ion thrusters will progress advanced deep space exploration.

# 5. Analysis

## 5.1. Summary of Proposed Improvements

Our project will produce the first working prototype for the RIOT Drive, and will include tasks such as:

- Electrostatic accelerator which can accumulate up to 100kV of potential on surface
- Shielding from the electric field to protect internal electronics
- Internal circuit board to supply power to all system components
- Material, geometry, and component selection for all systems
- Capability to withstand physical stresses of space launch

## 5.2. Disadvantages and Limitations

Potential limitations of the RIOT Drive project include:

- Many unknowns in performance as an emerging technology
- Inability to generate enough thrust to achieve liftoff on its own
- Limited ability to fully test prototypes due to no access to the ionizer chips
- Limitations in testing many components in vacuum conditions
- Many considerations for space readiness can not be tested, only modeled
- Small model may perform differently than full-size product

## 5.3. Alternatives

As space travel currently exists, there are many alternatives to the RIOT Drive. These include:

- Traditional fuel propulsion
  - Able to achieve liftoff and exit Earth’s gravity independently
  - Already a proven method
  - Significantly less fuel efficient and a much heavier fuel
  - Takes up significantly more aircraft space
- Current Ion Thrusters
  - Generally considered ineffective for spacecraft, except for long-term control or small adjustments
  - Uses a less efficient and much more expensive fuel, Xenon
  - Currently used for station-keeping

## 5.4. Impact

While ion thrusters are currently not viable for much more than slight adjustments in space, a working RIOT Drive will change that. Very few propulsion systems can compete with the delta-V that the RIOT Drive will provide, and it will become the preferred propulsion method for deep space missions. The significant reduction in fuel costs will make it more feasible to implement on satellites in ways that were too expensive or inefficient before. While this prototype will fit in a CubeSat, future systems will be larger, capable of creating enough thrust to be the main propulsion device of a large rocket or satellite once it reaches space. The RIOT Drive will allow us to send satellites further into space because of its high efficiency and speed, potentially leading to significant discoveries.

Concept of Operations Revision 1 Cubesat EM Material Discharge Eval

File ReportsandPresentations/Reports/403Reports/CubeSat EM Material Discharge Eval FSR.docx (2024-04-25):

CubeSat EM Material Discharge Eval

Joshua Feldman

Michael Kim

Ian Poynter

Alejandro Torres

Functional System Requirements

REVISION – Draft

28 September 2023

Functional System Requirements

for

CubeSat EM Material Discharge Eval

Prepared by:

_____________________________

Author Date

Approved by:

_____________________________

Project Leader Date

_____________________________

John Lusher, P.E. Date

_____________________________

T/A Date

Change Record

Rev. | Date | Originator | Approvals | Description
- | 9/28/2023 | Ian Poynter | | Draft Release
1 | 12/3/2023 | Ian Poynter | | End of Semester Revision

Table of Contents

Table of Contents 3

List of Tables 4

List of Figures 5

1. Introduction 6

1.1. Purpose and Scope 6

1.2. Responsibility and Change Authority 6

2. Applicable and Reference Documents 7

2.1. Applicable Documents 7

2.2. Reference Documents 7

2.3. Order of Precedence 7

3. Requirements 8

3.1. System Definition 8

3.2. Characteristics 9

3.2.1. Functional / Performance Requirements 9

3.2.1.1 Accelerator Plate….………………………………………………………………..9

3.2.1.2 Shielding………..….………………………………………………………………..9

3.2.1.3 Microcontroller….….………………………………………………………………..9

3.2.2. Physical Characteristics 9

3.2.3. Electrical Characteristics 10

3.2.4. Environmental Requirements 11

3.2.5. Failure Propagation 12

4. Support Requirements 13

Appendix A Acronyms and Abbreviations 14

Appendix B Definition of Terms 15

Appendix C Interface Control Documents 16

List of Tables

Table 1: Subsystems and Responsibility………………………………………………….6

Table 2: Applicable Documents……………………………………………………………..7

Table 3: Reference Documents…………………………………………………………...…7

List of Figures

Figure 1: Your Project Conceptual Image 1

Figure 2: Block Diagram of System 4

# 1. Introduction

## 1.1. Purpose and Scope

The purpose of this project is to design and build the prototype of the RIOT Drive that will have the capability to fit within 1U of a CubeSat with an emphasis on maintaining a low weight to reduce the costs for launch and maximize propulsion while in space. The prototype will be specifically designed to measure the data of different geometries and materials used to see the efficiency of each model. We will also design the power supply within the prototype to deliver power to the components of the RIOT Drive. Figure 1 shows a rough design of a modeled prototype with one of the geometries that is used.

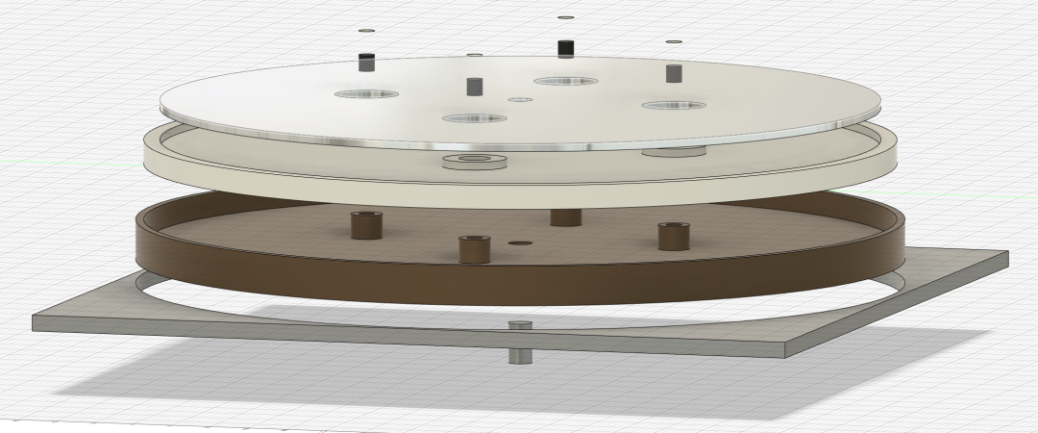
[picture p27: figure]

Figure 1: Model of Orbital Arc RIOT Drive

## 1.2. Responsibility and Change Authority

The team leader, Ian Poyner, is responsible for ensuring all requirements for the system are met. Changes made to each subsystem are to be approved by the team leader and Professor John Lusher. Subsystem responsibility is as follows:

Subsystem | Responsibility
High Potential Accelerator Modeling | Michael Kim
CubeSat Chassis Construction | Ian Poynter
Power Supply Circuit | Alejandro Torres
Microcontroller | Josh Feldman

Table 1: Subsystems and Responsibility

# 2. Applicable and Reference Documents

## 2.1. Applicable Documents

The following documents, of the exact issue and revision shown, form a part of this specification to the extent specified herein:

Document Number | Revision/Release Date | Document Title
19970027853 | Revision 4 - June 1997 | Outgassing Data for Selecting Spacecraft Materials
CP-CDS-R14.1 | Revision 14.1 - February 2022 | CubeSat Design Specifications

Table 2: Applicable Documents

## 2.2. Reference Documents

The following documents are reference documents utilized in the development of this specification. These documents do not form a part of this specification and are not controlled by their reference herein.

Document Number | Revision/Release Date | Document Title
20210018053 | July 1, 2021 | Avionics Radiation Hardware Assurance (RHA) Guidelines
19920003068 | September 1991 | NASA Reliability Preferred Practices for Design and Test
NPR 7120.10B | June 1, 2022 | Technical Standards for NASA Programs and Projects

Table 3: Reference Documents

## 2.3. Order of Precedence

In the event of a conflict between the text of this specification and an applicable document cited herein, the text of this specification takes precedence without any exceptions.

All specifications, standards, exhibits, drawings or other documents that are invoked as “applicable” in this specification are incorporated as cited. All documents that are referred to within an applicable report are considered to be for guidance and information only, except ICDs that have their relevant documents considered to be incorporated as cited.

# 3. Requirements

## 3.1. System Definition

Our project will be making the first functional prototype for the RIOT Drive, proposed by Orbital Arc. Our goal is to design power supply circuitry capable of delivering the necessary power to all components that would be present in a launch-ready system. We will also be collecting experimental data on the electric field produced by the different accelerator plate geometries and materials. Additional responsibilities include designing the microcontroller system to operate components such as the gas feed valve and pulse chargers, the design of the CubeSat chassis, and risk consideration calculations such as thermal, radiation, and outgassing.


Figure 2: Block Diagram of System

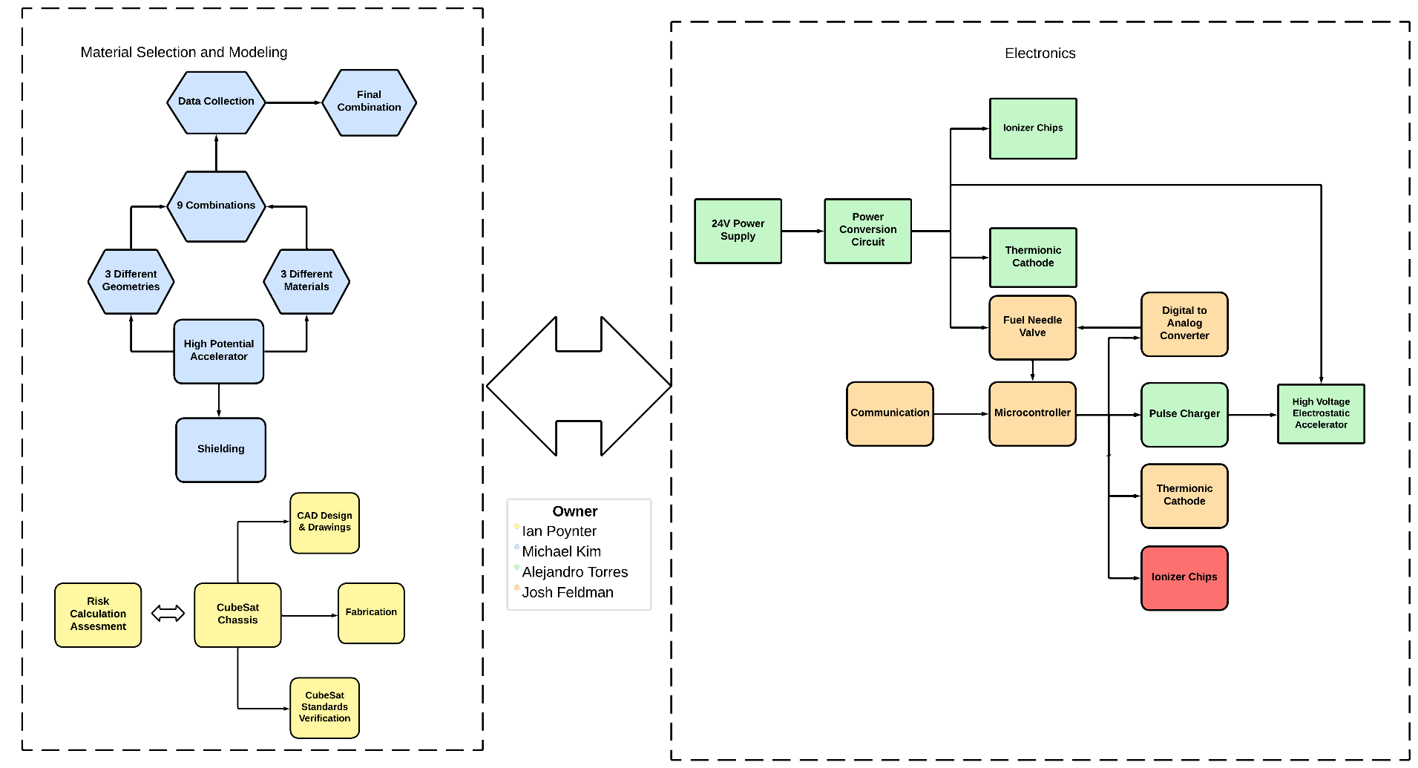
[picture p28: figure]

Figure 3: Expanded Block Diagram of Subsystems

The RIOT Drive prototype shall have 2 main components broken down into 2 subsystems each. The high potential accelerator shall include the construction of the plate that holds the high voltage for accelerating the ions, and shielding of the software from the voltage on the plate. This subsystem will interface with the chassis for mounting, the power circuit for charging the plate, and the microcontroller for enabling the plate and determining the amount of charge. The CubeSat chassis shall be constructed of material that can withstand space launch and travel. It will fit inside a CubeSat, and be constructed to mount the accelerator plate and shielding, and the power supply circuit. Ian Poynter will be creating the chassis out of aluminum 7075. The power supply circuit will take a 24VDC input and supply proper power to all components, including the pulse charger for the accelerator plate, the thermionic cathode, the ionizer, the gas feed control, and the microcontroller. The microcontroller will control charging the accelerator plate, the gas feed control, the ionizer, and the thermionic cathode.

## 3.2. Characteristics

### 3.2.1. Functional / Performance Requirements

#### 3.2.1.1. Accelerator Plate

The RIOT Drive accelerator shall sustain a charge of 40kV ±1% and reach up to 100 kV ±1% .

Rationale: This is the highest voltage our RIOT Drive would ever need, specified by Orbital Arc, so testing the maximum voltage ensures that lower voltages are sustainable.

#### 3.2.1.2. Shielding

The Accelerator shall be shielded from the electronics so the electronics can function without interference. Thermal and radiation shielding will need to be included in the internal electronics design.

Rationale: This is required by the project for the power circuit and microcontroller to function in a space environment.

      3.2.1.3. Microcontroller

The microcontroller shall be able to regulate gas flow of the fuel, enable the accelerator, and time the pulse charger for charging the accelerator plates.

Rationale: The microcontroller must interface with these components of the RIOT Drive for it to function properly.

### 3.2.2. Physical Characteristics

#### 3.2.2.1. Mass

The total mass of the CubeSat prototype shall not exceed 2 kg. The mass of the power supply circuit shall be less than or equal to 200 grams. The mass of the chassis shall not exceed 200 grams.

Rationale: The CubeSat total weight is specified by the CubeSat Design Specifications. The power supply weight is a requirement specified by our customer due to the size of the CubeSat and the power of the RIOT Drive.

#### 3.2.2.2. Volume Envelope

The volume envelope of the RIOT Drive shall be 10 cm in height, 10 cm in width, and 10 cm in length. The volume envelope of the power supply circuit shall be less than or equal to 2 cm in height, 10 cm in width, and 10 cm in length. Certain parts of the design, such as the battery or fuel tank, will be considered to be external to the 1U CubeSat. The chassis shall also undergo strength testing to ensure structural integrity.

Rationale: This is a requirement specified by our customer due to constraints of a CubeSat which the RIOT Drive shall fit inside.

#### 3.2.2.3. Mounting

The mounting information for the RIOT Drive shall be designed to interface with a common CubeSat frame design.

Rationale: This is a requirement specified by our customer due to the constraint of needing to be mounted inside a CubeSat.

#### 3.2.2.4. Accelerator Geometry and Material

The geometry and material for the RIOT Drive High Potential accelerator will be chosen from one of the tested combinations of 3 different geometries and 3 different materials.

Rationale: This is to test out which combination can meet the required tasks and objectives of optimization of the accelerator the best.

### 3.2.3. Electrical Characteristics

#### 3.2.3.1. Inputs

a. The presence or absence of any combination of the input signals in accordance with ICD specifications applied in any sequence shall not damage the RIOT Drive, or cause any malfunction, either when the unit is powered or when it is not.
b. No sequence of command shall damage the RIOT Drive, or cause any malfunction.

Rationale: By design, should limit the chance of damage or malfunction by user/technician error.

##### 3.2.3.1.1 Power Consumption

a. The maximum peak power of the system shall be 50 watts.

Rationale: This is a requirement specified by our customer due to the power demands of their system.

##### 3.2.3.1.2 Input Voltage Level

The input voltage level for the RIOT Drive shall be 24V ±1% .

Rationale: This is a requirement specified by our customer due to the supply from the spacecraft

##### 3.2.3.1.3 External Commands

The RIOT Drive system shall document all external commands in the appropriate ICD.

Rationale: The ICD will capture all interface details from the low-level electrical to the high-level packet format.

#### 3.2.3.2. Outputs

        3.2.3.2.1 Output Levels
b. The output voltage level of the accelerator plate shall reach a maximum of 100kV.
c. The output of the power supply circuit shall be as follows:
  i. 3-12V for the High Voltage Electrostatic Accelerator
  ii. 33V for the Ionizer Chips
  iii. 3-6V for the Thermionic Cathode
  iv. 5V/3.3V for the Microcontroller

Rationale: This is a requirement specified by the customer

##### 3.2.3.2.2 Diagnostic Output

The RIOT Drive prototype is designed as a proof of concept and will not include a diagnostic interface for debugging. Debugging shall be handled by an oscilloscope.

Rationale: This project is a prototype and building a diagnostic interface is outside the scope of this project.

#### 3.2.3.3. Wiring

The RIOT Drive’s wiring will be done on a PCB design.

Rationale: The PCB design will provide stability to the system.

### 3.2.4. Environmental Requirements

The RIOT Drive shall be designed to withstand and operate in the environments and laboratory tests specified in the following section.

Rationale: This is a requirement specified by our customer due to constraints of their system in which the Search and Rescue System is integrating.

#### 3.2.4.1. Space Launch

The RIOT Drive’s power supply shall be designed to withstand the physical stresses of space launch.

Rationale: The RIOT Drive is intended to be launched in space, so the system will have to withstand physical pressures that are caused during space launch.

#### 3.2.4.2. Thermal

The RIOT Drive’s power supply shall be designed to withstand the thermal stresses from space and space launch. Component selection will also take into consideration thermal effects.

Rationale: The RIOT Drive will be in space, so it must withstand any temperatures that will be reached in outer space

#### 3.2.4.3. Outgassing in Vacuum

The materials exposed in outer space shall have TML must be less than 1% and the CVCM must be less than 0.1% as specified by document 19970027853.

Rationale: This is a constraint provided by NASA’s requirements for material outgassing in outer space.

### 3.2.5. Failure Propagation

By following safe coding practices, any exceptions will be caught and will throw errors if the system cannot recover. The system will be tested rigorously to ensure that the code functions properly for the prototype. As this system is only a prototype and lacks many features that will be designed by Orbital Arc, Built In Testing is beyond the scope of this project.

# 4. Support Requirements

For our prototype, support will be provided to Orbital Arc through documentation such as the Functional System Requirements and Interface Control Document. In the future, users will be provided with support through instruction documents from Orbital Arc and meetings with Orbital Arc and the consumer company to discuss how the RIOT Drive will be used. Electronic support will be implemented through the on-board computers of the spacecraft.

# d. Appendix A: Acronyms and Abbreviations

kV kilovolts (1000 Volts)

VDC Volts Direct Current

ICD Interface Control Document

RIOT Relativistic Ion Thrust

TML Total Mass Loss

CVCM Collected Volatile Condensable Material

1U 1 unit

# e. Appendix B: Definition of Terms

CubeSat: A standard set by Cal Poly, the CubeSat platform standardizes nanosatellites into a 10cm x 10cm x 10cm cube (1U) for delivering payloads to outer space.

Calibrated LWIR Raw Video Data Collection - Gold Standard – Test 1 Revision -

Functional System Requirements Revision - 1 CubeSat EM Material Discharge Eval

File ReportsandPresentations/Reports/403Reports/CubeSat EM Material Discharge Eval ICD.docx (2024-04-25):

CubeSat EM Material Discharge Eval

Joshua Feldman

Michael Kim

Ian Poynter

Alejandro Torres

Interface Control Document

REVISION – Draft

28 September 2023

Interface Control Document

for

CubeSat EM Material Discharge Eval

Prepared by:

_____________________________

Author Date

Approved by:

_____________________________

Project Leader Date

_____________________________

John Lusher II, P.E. Date

_____________________________

T/A Date

Change Record

Rev. | Date | Originator | Approvals | Description
- | 9/28/2023 | Ian Poynter | | Draft Release
1 | 12/3/2023 | Ian Poynter | | End of Semester Revision

Table of Contents

Table of Contents 3

List of Tables 4

List of Figures 5

1. Overview 6

2. References and Definition 7

2.1. References 7

2.2. Definitions 7

3. Physical Interface 8

3.1. Weight 8

3.2. Dimensions 8

3.2.1 Dimensions of Accelerator Plate…………………………………………………………8

3.2.2 Dimensions of CubeSat Apparatus……………………………………………………... 8

3.2.3 Dimensions of Power Supply Circuitry..…………………………………………………8

3.3. Mounting Locations 9

3.3.1 CubeSat Mounting…………………………………………………………………………9

3.3.2 Accelerator Plate Mounting …………………………………………………..………..…9

3.3.3 Power Supply Mounting…………………………………..……………………………… 9

4. Thermal Considerations 10

4.1. Cooling of Internal Electronics 10

5. Electrical Interface 11

5.1. Primary Input Power 11

5.2. Voltage and Current Levels 12

5.3. Signal Interfaces 12

5.4. User Control Interfaces 12

6. Communications / Device Interface 13

6.1 Prototype Interface 13

6.2. Use in Spacecraft .….13

List of Tables

Table 1: Approximate Weight Distribution of Subsystems……………………8

Table 2: Power Supply Circuitry Dimensions……………………………….....8

Table 3: Voltage and Power for Components……………………………….. 12

List of Figures

# 1. Figure 1: Breakdown of the Power Supply Subsystem……………………..12

# 4. Overview

The Interface Control Document (ICD) provides detailed information about the RIOT Drive and outlines the technical requirements for each subsystem. This document will provide an in-depth description of the physical, thermal, electrical, and communication interfaces of the RIOT Drive.

# 5. References and Definitions

## 5.1. References

19970027853 Outgassing Data for Spacecraft Material Selection

June 1997

Revision 4

CP-CDS-R14.1 CubeSat Design Specifications (CDS)

February 2022

Revision 14.1

p237 MATERIALS FOR ACCELERATOR VACUUM SYSTEMS

May 1999

20210018053 Avionics Radiation Hardware Assurance (RHA) Guidelines

July 2021

## 5.2. Definitions

PCB Printed Circuit Board

A Amp

W Watt

V Volt

TBD To Be Determined

cm Centimeter

kg Kilogram

CubeSat A 10cm x 10cm x 10cm cube for payloads to outer space

1U 1 unit (typically of a CubeSat)

ADC Analog to Digital Converter

DAC Digital to Analog Converter

# 6. Physical Interface

The RIOT Drive prototype shall be designed to fit inside a 1U CubeSat, with an emphasis on maintaining a low weight to reduce costs for launch and maximize propulsion while in space.

## 6.1. Weight

Below is the approximate weight distribution of the subsystems. Hard requirements include a power supply weight of no more than 200 grams, and a total weight of under 2 kg.

Component | Target Weight (kg)
Power Supply | <0.2
Chassis | <0.2
Accelerator Plate | ~1
Total | <2

Table 1: Approximate weight distribution of subsystems

## 6.2. Dimensions

### 6.2.1. Dimensions of Accelerator Plate

For the Accelerator Plates, we will be testing 3 different geometries and 3 different materials, giving 9 total different combinations. The geometries include a circular plane, a hemisphere, and a cone. All geometries will meet the size requirement, which is less than a face of a 10 cm cube. The materials include: Teflon, Polypropylene, and High Density Polyethylene. These materials can handle a high-stress rate, vacuum, radiation, and electromagnetic field. We will then choose which of the three combinations will be used in our final project.

    6.2.2. Dimensions of CubeSat Apparatus

The apparatus for the CubeSat shall comply with the requirements in the CubeSat Design Specifications (CDS) set forth by California Polytechnic State University. The external measurements of the CubeSat shall not exceed a 10 cm cube and shall weigh less than 2 kg.

    6.2.3. Dimensions of Power Supply Circuit

Component | Length (cm) | Width (cm) | Height (cm)
Power Converter Circuit | ~10 | ~10 | <2

Table 2: Power Supply Circuitry Dimensions

## 6.3. Mounting Locations

    6.3.1. CubeSat Mounting

One characteristic of the CubeSat platform is the configurability to connect multiple CubeSats to form larger satellites. While our RIOT Drive prototype will function within one unit of a CubeSat, additional CubeSats may be connected for a space test to include the battery and fuel tank. Because of this, our prototype must be compatible to mount with other CubeSat units.

    6.3.2. Accelerator Plate Mounting

The accelerator plate prototypes shall be able to mount within a 1U CubeSat. Accelerator plates used for testing may not be configured to mount on the CubeSat chassis, but the final design chosen for material and geometry will mount on a vertical face (top/bottom) of the CubeSat.

    6.3.3. Power Supply Mounting

The power supply will be mounted internally in the Cubesat. The exact location of the power supply within the satellite will be chosen so that it evenly distributes the weight from it and other components equally. This will allow the satellite to deliver balanced thrust and maintain appropriate trajectories when used in space. The microcontroller system will be set up on the same PCB as the power supply routing.

# 7. Thermal Interface

Thermal considerations shall be taken into account throughout the design process of the CubeSat RIOT Drive prototype due to the requirement for operation in space. With the extreme cold of space, the system will need to be insulated to prevent issues with the temperature. With a power output near 50 W for the power supply circuit, the heat from the circuitry will need to be managed and dispersed. Losses due to heat in the circuit may be used to maintain a desirable ambient temperature for circuitry or other components inside the CubeSat.

## 7.1. Cooling of Internal Electronics

Due to the significant power output of the internal electronics, the heat will need to be dissipated. Heatsinking will occur from high-power components of the internal electronics and will be connected to the CubeSat chassis. The extremely cold temperatures of space will be used to manage the temperature, while the dissipation of heat will serve to maintain an acceptable ambient temperature internally.

# 9. Electrical Interface

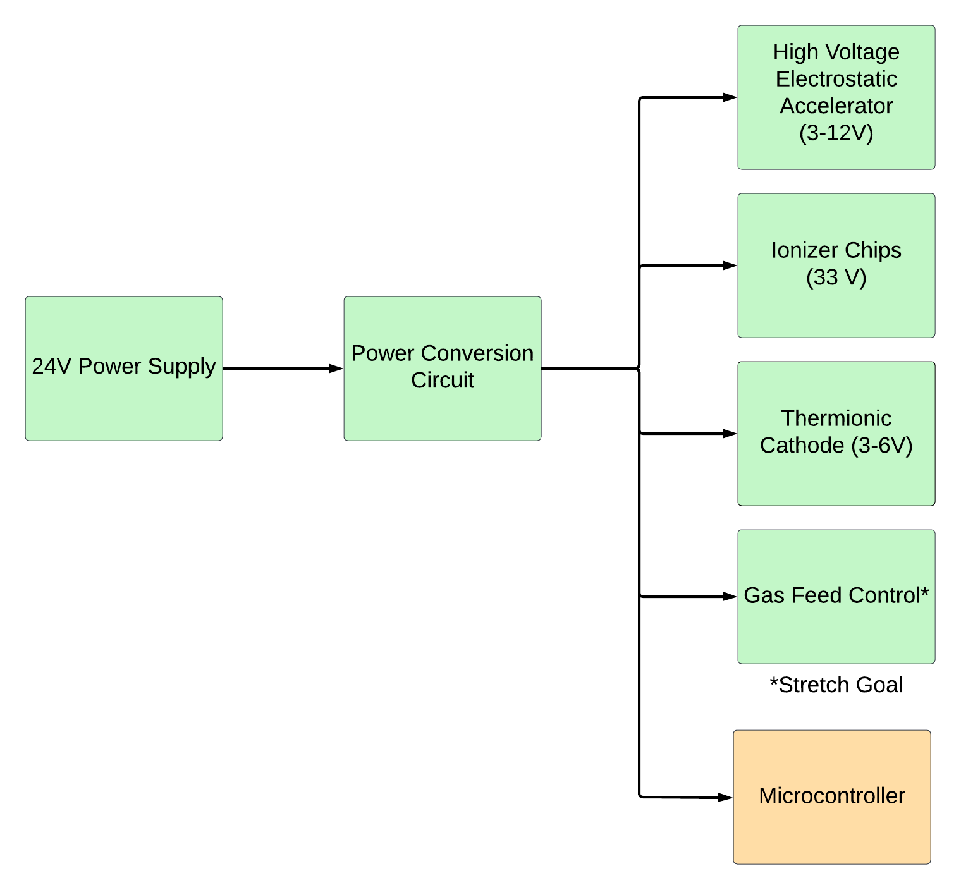
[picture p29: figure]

Figure 1: Breakdown of the Power Supply Subsystem

Figure 1 shows how the electrical interface of the RIOT Drive shall work. The 24V power supply shall go through a voltage converter and supply the voltages to the components as shown in Figure 1.

## 9.1. Primary Input Power

The primary input power that would provide power to the CubeSat would be the spacecraft, assuming it would provide a voltage of 24 VDC. The power budget for the power supply shall be 25 W plus the power for the ionizer chip.

## 9.2. Voltage and Current Levels

The power supply system shall be designed to output the required power and voltage criteria for the components within the CubeSat. The table below lists the necessary voltage and power requirements needed from the power supply circuit to provide power to the necessary components for the CubeSat.

Component | Voltage (V) | Current (A) | Power (W)
High Voltage Electrostatic Accelerator | 3-12 | N/A | N/A
Thermionic Cathode | 3-6 | 0.3-1 | 1-3
Ionizer Chips | 33 | 0.62 | ~21
Digital-to-Analog Converter | 3.3 | 0.3 | 1
Microcontroller | 3.3 | 0.3 | 1

Table 3: Voltage and Power for Components

## 9.3. Signal Interfaces

The microcontroller shall be mounted on a PCB, and shall be wired to controls for the pulse charger, thermionic cathode, ionizer chips. The gas feed control will be compared by an ADC, and the output value will be transmitted to the gas feed control by the DAC.

## 9.4. User Control Interface

No user interface was specified as required by the customer because the project is a prototype to prove that the RIOT Drive accelerator, shielding, and power circuit functions.

# 10. Communications / Device Interface Protocols

## 10.1. Prototype Interface

Our prototype will have parts of the system, such as the gas feed valve and high-voltage pulser, interface and communicate with the microcontroller. The circuit board will have test points for voltage probes in critical locations for the user to identify issues with the performance. A space-ready prototype would include a communication system which would be housed inside another CubeSat unit, and is outside the scope of our design.

## 10.2. Use in Spacecraft

While our prototype will have an internal microcontroller, commercialized systems of the RIOT Drive would rely on the onboard computers of the spacecraft for system control.

Interface Control Document Revision - 1 CubeSat EM Material Discharge Eval

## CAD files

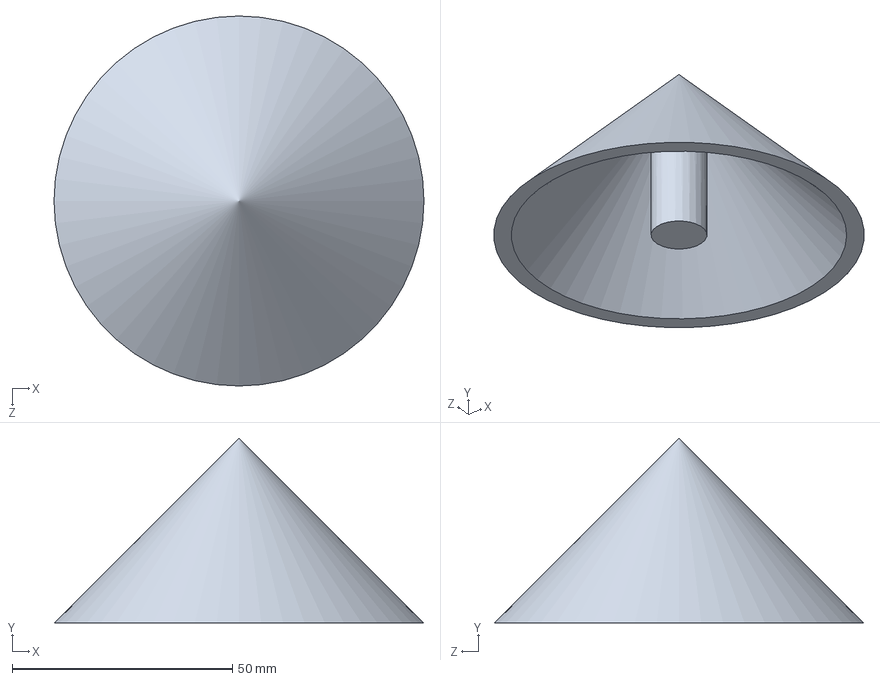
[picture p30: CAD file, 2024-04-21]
AcceleratorModeling/Solidworks/Cone/InsulatorCone.SLDPRT
84.0 x 42.0 x 84.0 mm

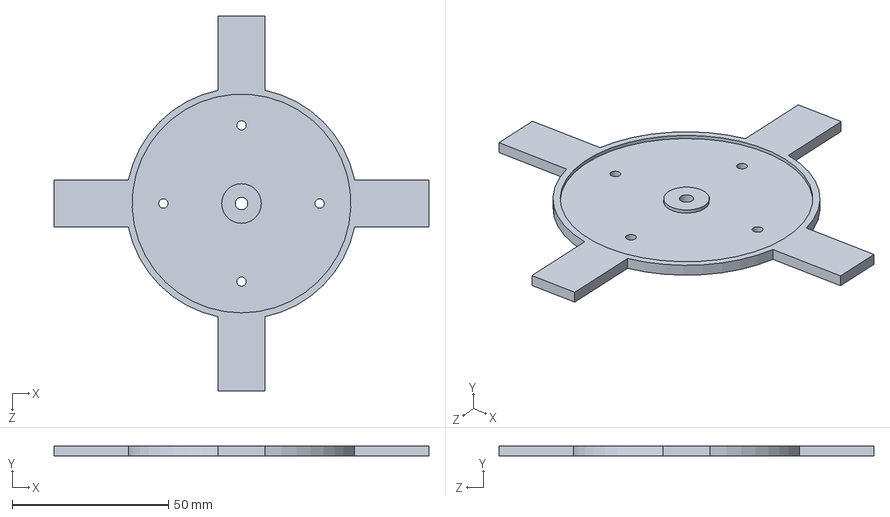
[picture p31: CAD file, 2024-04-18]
AcceleratorModeling/Solidworks/FinalAcceleratorPlate/FinalInsulatorPieceVer2.SLDPRT
120.0 x 3.16 x 120.0 mm

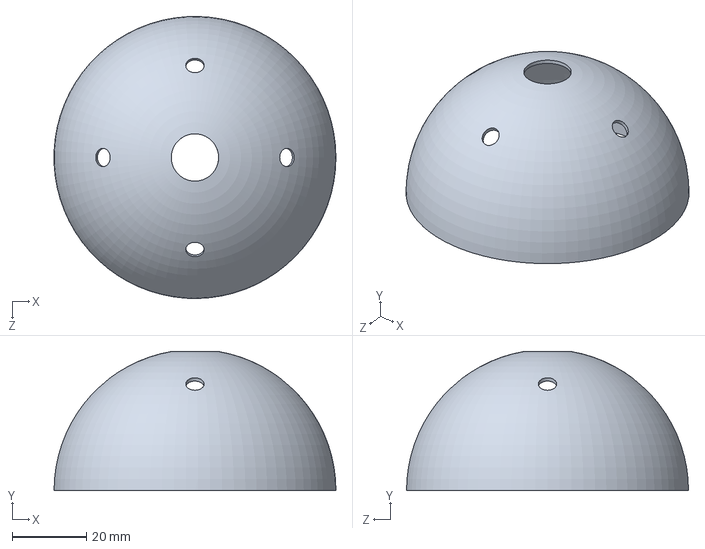
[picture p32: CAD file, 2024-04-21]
AcceleratorModeling/Solidworks/Hemisphere/MetalHemisphere.SLDPRT
75.9 x 37.4 x 75.9 mm

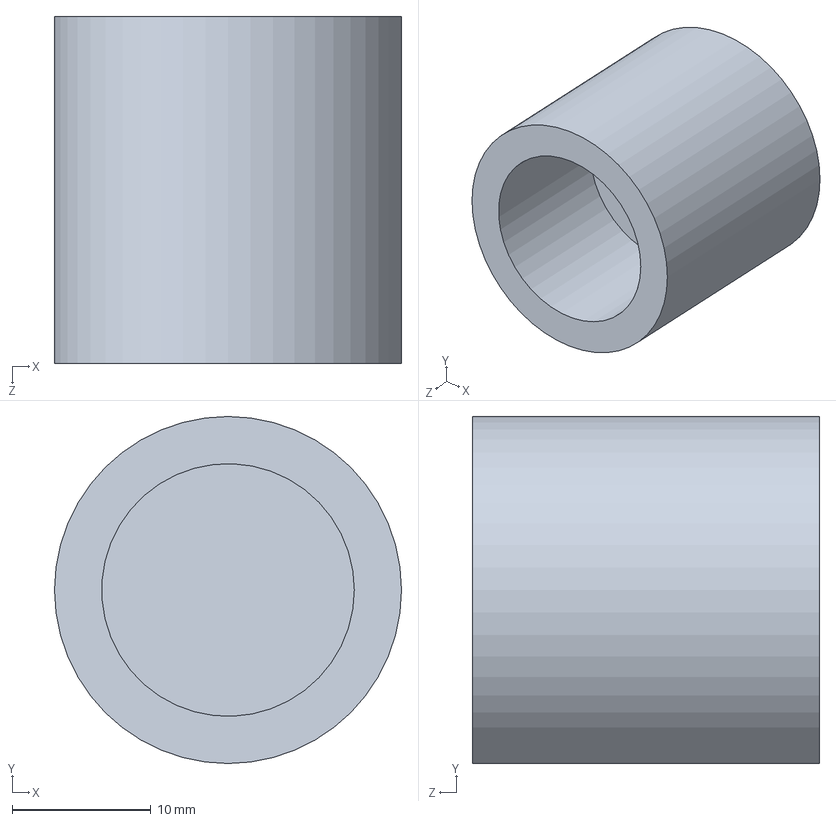
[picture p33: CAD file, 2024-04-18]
ChassisandModeling/Chassis File/MotorConnector.SLDPRT
25.0 x 25.0 x 25.0 mm

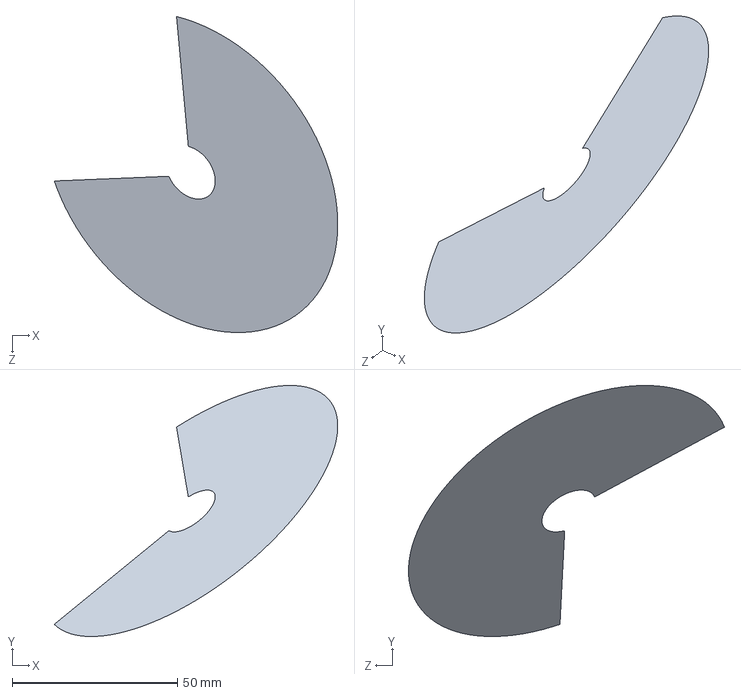
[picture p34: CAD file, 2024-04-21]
AcceleratorModeling/Solidworks/Cone/MetalConeFlat.SLDPRT
85.8 x 76.0 x 95.6 mm

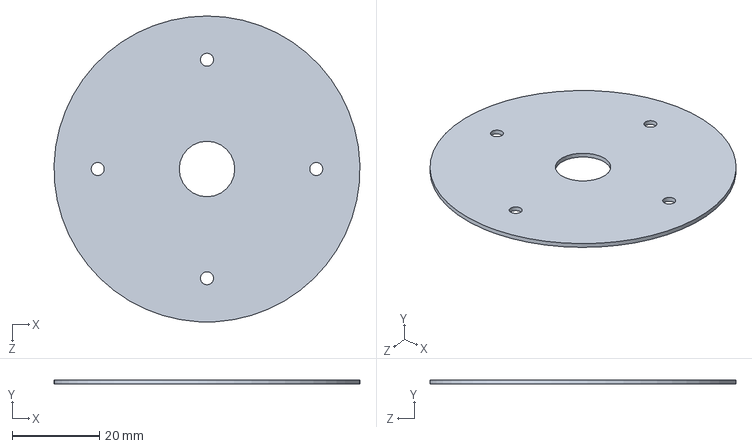
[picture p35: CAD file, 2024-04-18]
AcceleratorModeling/Solidworks/FinalAcceleratorPlate/FinalMetalPiece.SLDPRT
70.0 x 1.00 x 70.0 mm

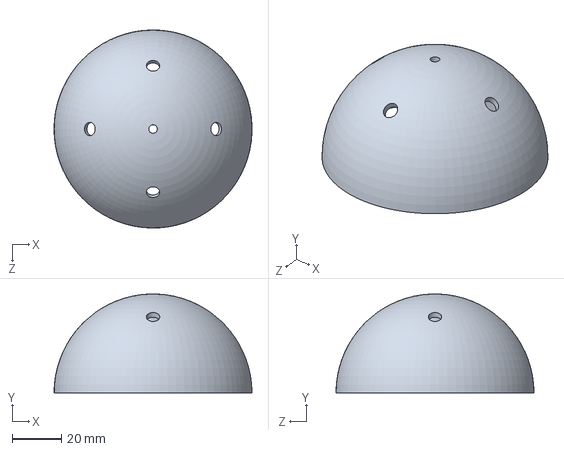
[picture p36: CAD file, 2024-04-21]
AcceleratorModeling/Solidworks/Hemisphere/InsulatorHemisphere.SLDPRT
80.5 x 40.3 x 80.6 mm

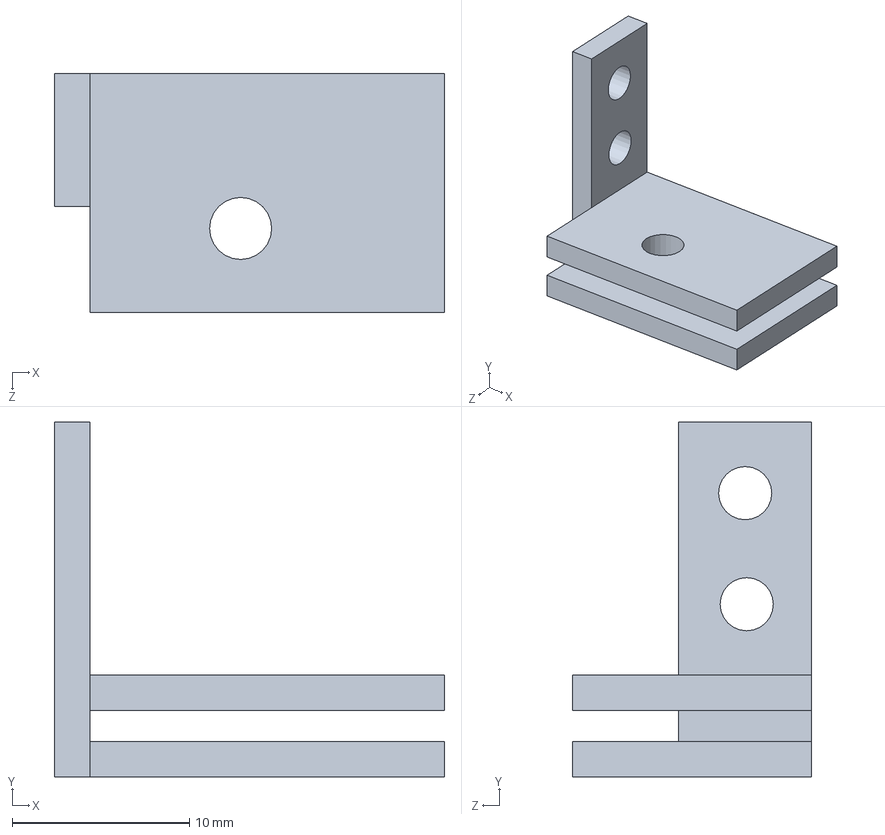
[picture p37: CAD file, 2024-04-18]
ChassisandModeling/Chassis File/PCBMounting_Side2.SLDPRT
22.0 x 20.0 x 13.5 mm

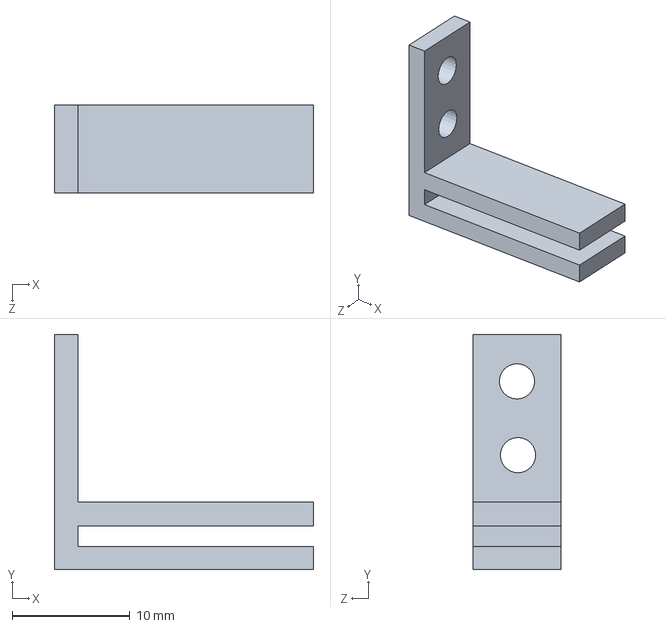
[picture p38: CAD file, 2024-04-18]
ChassisandModeling/Chassis File/PCBMounting_1.SLDPRT
22.0 x 20.0 x 7.50 mm

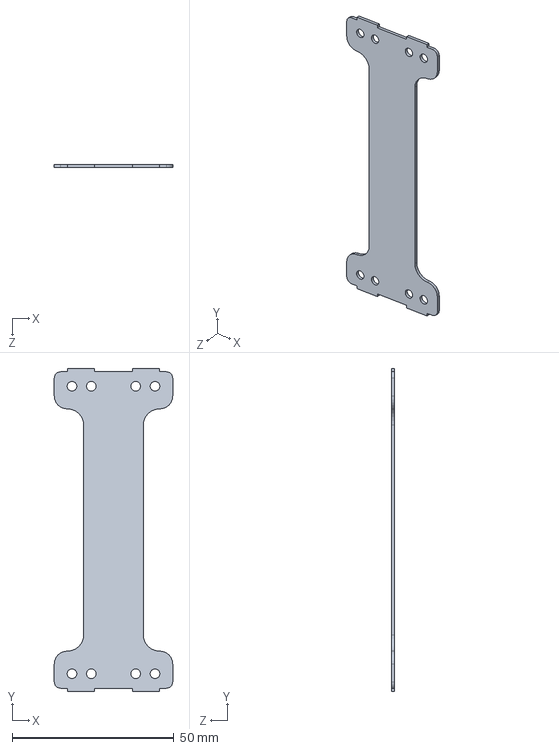
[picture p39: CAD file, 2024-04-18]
ChassisandModeling/Chassis File/ChassisCorner.SLDPRT
36.7 x 100.0 x 1.00 mm

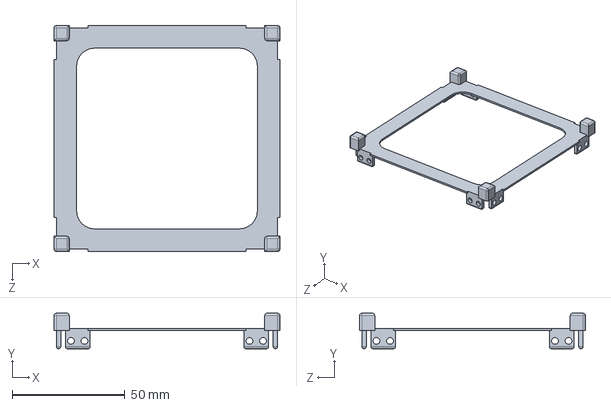
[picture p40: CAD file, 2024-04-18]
ChassisandModeling/Chassis File/ChassisTop.SLDPRT
100.0 x 15.8 x 100.0 mm

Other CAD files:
ChassisandModeling/Chassis File/PCBMounting_Hole.SLDPRT
ChassisandModeling/Chassis File/ChassisCorner_Flat.SLDPRT
ChassisandModeling/Chassis File/Corner1_Mount.STL
ChassisandModeling/Chassis File/PCBMounting_Side1.SLDPRT
ChassisandModeling/Chassis File/PCBMounting_NoHole.SLDPRT
ChassisandModeling/Chassis File/Corner2_Mount.STL
AcceleratorModeling/Solidworks/FinalAcceleratorPlate/FinalInsulatorPieceVer2.SLDDRW
AcceleratorModeling/Solidworks/FinalAcceleratorPlate/FinalMetalPiece.SLDDRW
AcceleratorModeling/Solidworks/Hemisphere/InsulatorHemisphere.SLDDRW
AcceleratorModeling/Solidworks/Hemisphere/MetalHemisphere.SLDDRW
ChassisandModeling/Chassis File/ChassisCorner.SLDDRW
ChassisandModeling/Chassis File/ChassisCorner_Flat.DXF
ChassisandModeling/Chassis File/ChassisCorner_Flat.SLDDRW
ChassisandModeling/Chassis File/ChassisTop.SLDDRW
ChassisandModeling/Chassis File/MotorConnector.STL
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

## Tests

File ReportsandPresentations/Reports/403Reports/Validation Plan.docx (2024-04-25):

Validation Plan

Paragraph | Task | Specification | Completed | Responsible Engineer
3.2.3.1.1 Power Consumption | Max Power | Measure power for each component ensuring below power budget of 50W | Incomplete | Alejandro Torres
3.2.3.1.2 Input Voltage Level | Voltage Supply | Voltage supply is 24 V | Completed | Alejandro Torres
3.2.3.2.1 Output Voltages | Microcontroller Supply Voltage | Microcontroller is supplied a voltage of 3.3V/5V | Completed | Alejandro Torres
3.2.3.2.1 Output Voltages | Thermionic Cathode Supply Voltage | Supplied Voltage between 3-6V | Completed | Alejandro Torres
3.2.3.2.1 Output Voltages | Ionizer Chips Supply | 33V Supplied | Incomplete | Alejandro Torres
3.2.3.2.1 Output Voltages | Output Voltage | Measure output voltages to be supplied for each component | Completed | Alejandro Torres
3.2.3. Dimensions of Power Supply | PCB Design | width & length : <100cm height: <20cm | Completed | Alejandro Torres
3.1 Weight | PCB Design | <0.2 kg | Completed | Alejandro Torres
3.2.2.2 Volume Envelope | Prototype Footprint | Footprint of our prototype fits CubeSat size regulations (10x10x10 cm) | Completed | Ian Poynter
3.2.2.1 Mass | Prototype Weight | Weight of the Chassis does not exceed 200 g on its own | Completed | Ian Poynter
3.2.2.3 Mounting | Electronics Mounting | Power Supply and Microcontroller PCB has space for mounting to the chassis | Completed | Ian Poynter
3.2.2.3 Mounting | Accelerator Plate Mounting | Mounting for accelerator plate is available and not blocked by chassis | Completed | Ian Poynter
3.2.2.2 Volume Envelope | CubeSat Regulations | The prototype chassis fits all CubeSat standards not neglected due to design restraints or to be tested in the future | Completed | Ian Poynter
3.2.2.4 Accelerator Geometry and Material | Geometry (Volume) | Accelerator will have around similar volume as desired volume (10 cm x 10 cm x ~2cm) to fit inside chassis | Completed | Michael Kim
3.2.2.4 Accelerator Geometry and Material | Geometry (Shape) | 3 geometries will extend retention without additional charging and protect spacecraft/ionizer from it | Completed | Michael Kim
3.2.2.4 Accelerator Geometry and Material | Material | 3 materials that handle space launch, radiation stress, and electric flux from space plasma will be tested | Completed | Michael Kim
3.2.2.4 Accelerator Geometry and Material | Combinations | All 9 combinations will be constructed for testing for electrostatic potential. | In Progress | Michael Kim
5.3 Signal Interfaces | Fuel Valve | Verify microcontroller compares and regulates fuel pressure and flow. | - | Joshua Feldman
5.3 Signal Interfaces | Microcontroller | Verify microcontroller properly activates pulse charger, ionizer, and thermionic cathode. | - | Joshua Feldman
5.3 Signal Interfaces | Microcontroller | All connections to the microcontroller are properly set up. | - | Joshua Feldman
6.1 Prototype Interface | Microcontroller | Microcontroller can be tested with test bench | - | Joshua Feldman
6.1 Prototype Interface | Microcontroller | BIT system properly catches exceptions thrown. | - | Joshua Feldman

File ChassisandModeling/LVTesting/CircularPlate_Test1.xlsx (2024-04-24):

Testing Voltage: | 25 V
Measured Voltage | 25.2 V
Designed Test
Percent Discharge | Time to Reach (ms) | Voltage (V)
5% | 4.32 | 23.9
10% | 9.84 | 22.7
15% | 16.56 | 21.4
20% | 21.2 | 20.2
25% | 27.6 | 18.9
35% | 39.12 | 16.4
50% | 61.2 | 12.6
75% | 97.2 | 6.3
Supply-to-Plate
Percent Discharge | Time to Reach (ms) | Voltage (V)
5% | 6.2 | 23.9
10% | 11.8 | 22.7
15% | 18.2 | 21.4
20% | 24.2 | 20.2
25% | 32.2 | 18.9
35% | 44.6 | 16.4
50% | 65 | 12.6
75% | 101.8 | 6.3

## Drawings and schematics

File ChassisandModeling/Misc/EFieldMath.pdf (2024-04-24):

# Circular Plate Math

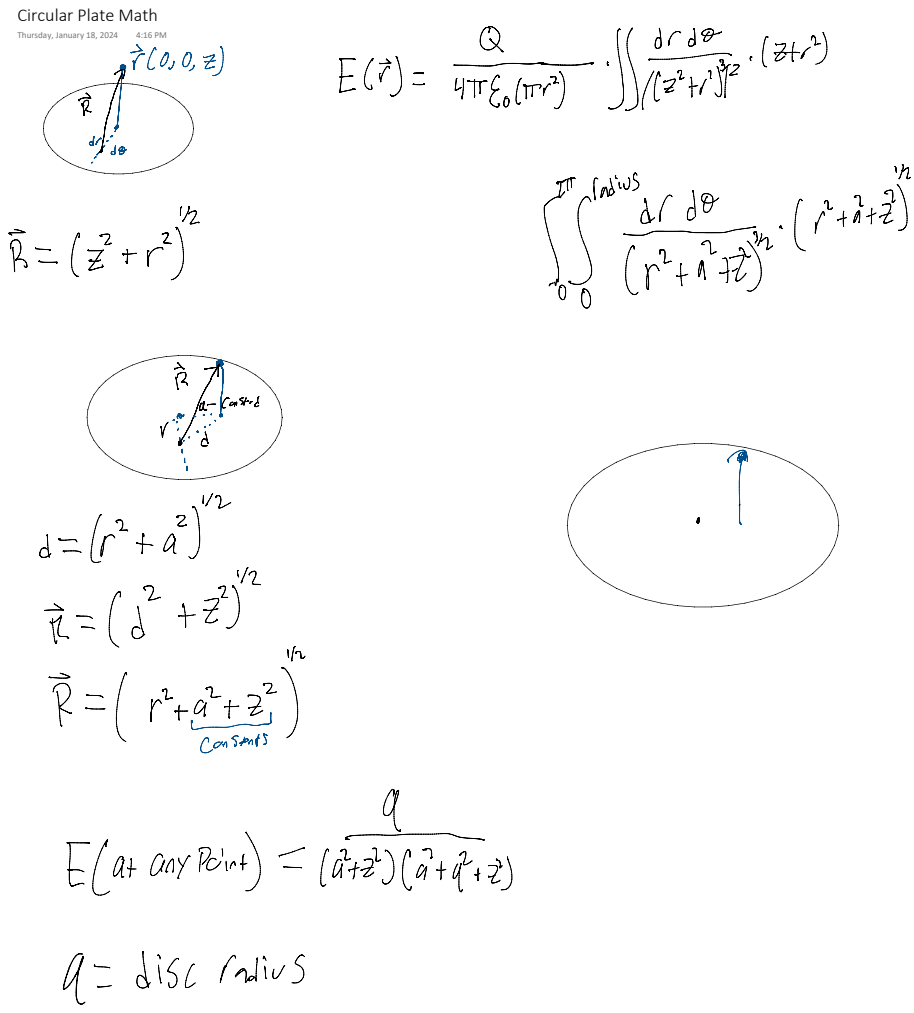
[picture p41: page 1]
Thursday, January 18, 2024

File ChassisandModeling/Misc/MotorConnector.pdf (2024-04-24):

# Motor Connector

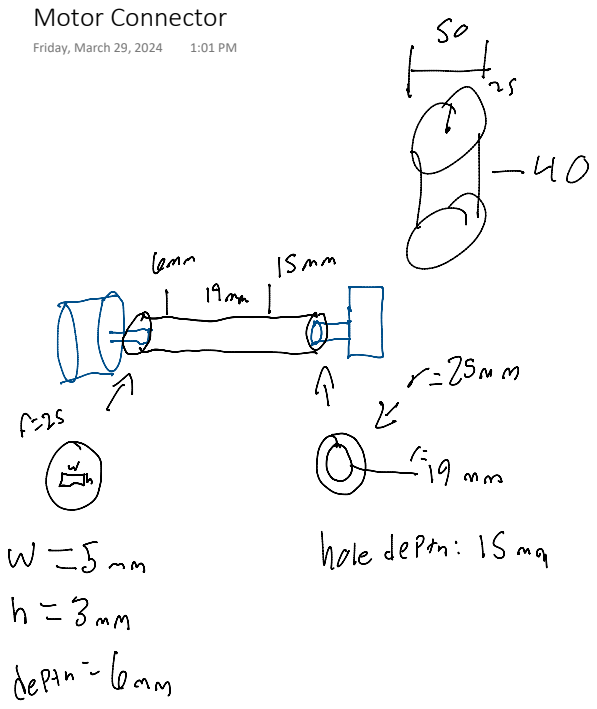
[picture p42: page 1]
Friday, March 29, 2024

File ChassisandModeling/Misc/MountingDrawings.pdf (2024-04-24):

# Mounting Design

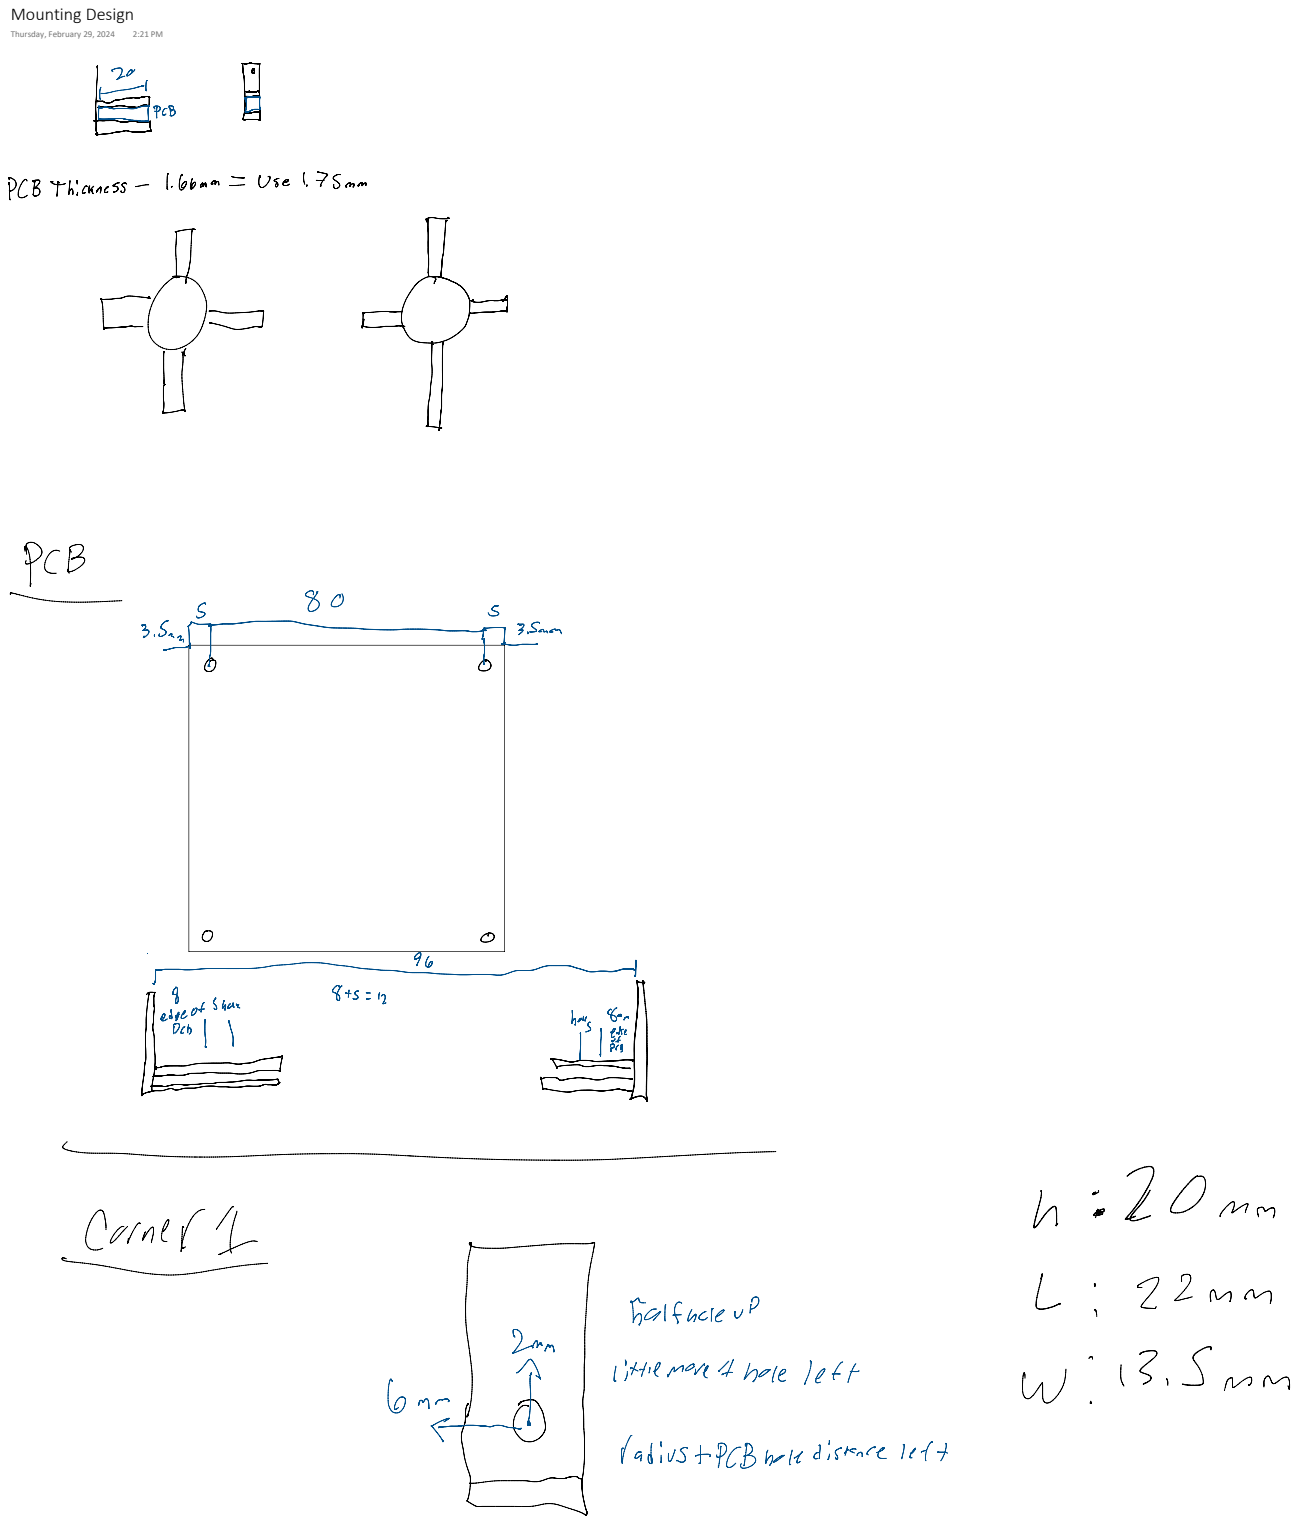
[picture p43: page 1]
Thursday, February 29, 2024

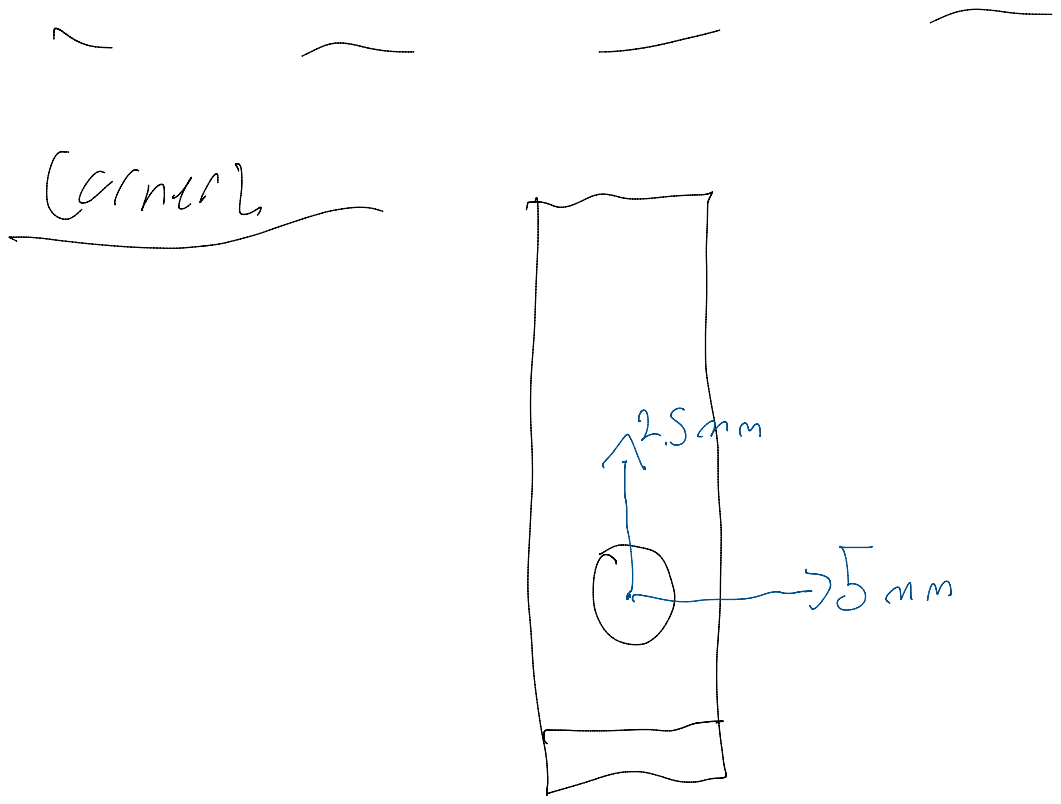
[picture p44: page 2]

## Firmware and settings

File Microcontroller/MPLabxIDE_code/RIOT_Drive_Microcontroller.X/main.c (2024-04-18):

/**
  Generated Main Source File

  Company:
    Microchip Technology Inc.

  File Name:
    main.c

  Summary:
    This is the main file generated using PIC10 / PIC12 / PIC16 / PIC18 MCUs

  Description:
    This header file provides implementations for driver APIs for all modules selected in the GUI.
    Generation Information :
        Product Revision  :  PIC10 / PIC12 / PIC16 / PIC18 MCUs - 1.81.8
        Device            :  PIC18F24Q10
        Driver Version    :  2.00
*/

/*
    (c) 2018 Microchip Technology Inc. and its subsidiaries. 
    
    Subject to your compliance with these terms, you may use Microchip software and any 
    derivatives exclusively with Microchip products. It is your responsibility to comply with third party 
    license terms applicable to your use of third party software (including open source software) that 
    may accompany Microchip software.
    
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
    IN NO EVENT WILL MICROCHIP BE LIABLE FOR ANY INDIRECT, SPECIAL, PUNITIVE, 
    INCIDENTAL OR CONSEQUENTIAL LOSS, DAMAGE, COST OR EXPENSE OF ANY KIND 
    WHATSOEVER RELATED TO THE SOFTWARE, HOWEVER CAUSED, EVEN IF MICROCHIP 
    HAS BEEN ADVISED OF THE POSSIBILITY OR THE DAMAGES ARE FORESEEABLE. TO 
    THE FULLEST EXTENT ALLOWED BY LAW, MICROCHIP'S TOTAL LIABILITY ON ALL 
    CLAIMS IN ANY WAY RELATED TO THIS SOFTWARE WILL NOT EXCEED THE AMOUNT 
    OF FEES, IF ANY, THAT YOU HAVE PAID DIRECTLY TO MICROCHIP FOR THIS 
    SOFTWARE.
*/

#include "mcc_generated_files/mcc.h"
#include <string.h>

#define MAX_CMD_LEN 8
#define clockwise 0
#define counter_clockwise 1

/*
    Variables 
*/

int c;
char data;
char command[MAX_CMD_LEN];
char prev_command[MAX_CMD_LEN];
int index;
int steps;
int i;
//unsigned int ADC_result;
//float voltage;
const uint8_t speed = 3; // Used to regulate speed of stepper motor



/*
    Functions 
 */

//void LoadDAC(uint16_t d) { //SPI for DAC
//uint16_t dac;
//
//dac = d | 0x3000;  //Insert command DACA, unbuffered, G = 1, output ON
//SSP1CON1 = 0x20;   //Enabled, Fosc/4, CKP = 0
//CS_SetLow(); // Enable transfer
//SSP1BUF = (unsigned char)(dac >> 8); // Put bits in buffer
//while(!PIR3bits.SSP1IF); // Check if transfer complete
//SSP1BUF = (unsigned char)(dac & 0x00ff);
//while(!PIR3bits.SSP1IF);
//CS_SetHigh();
//SSP1CON1 = 0x00;  //Disabled
//}

void full_drive(uint8_t dir) {  // Code adapted from circuitdigest.com
    if(dir == clockwise){

        Drive_A_SetHigh();  //1100
        Drive_B_SetHigh();
        Drive_C_SetLow();
        Drive_D_SetLow();
        __delay_ms(speed);
        
        Drive_A_SetLow();   //0110
        Drive_B_SetHigh();
        Drive_C_SetHigh();
        Drive_D_SetLow();
        __delay_ms(speed);
        
        Drive_A_SetLow();   //0011
        Drive_B_SetLow();
        Drive_C_SetHigh();
        Drive_D_SetHigh();
        __delay_ms(speed);
        
        Drive_A_SetHigh();  //1001
        Drive_B_SetLow();
        Drive_C_SetLow();
        Drive_D_SetHigh();
        __delay_ms(speed);
        
        Drive_A_SetHigh();  //1100
        Drive_B_SetHigh();
        Drive_C_SetLow();
        Drive_D_SetLow();

    }

    if(dir == counter_clockwise) {

        Drive_A_SetHigh();  //1001
        Drive_B_SetLow();
        Drive_C_SetLow();
        Drive_D_SetHigh();
        __delay_ms(speed);
        
        Drive_A_SetLow();   //0011
        Drive_B_SetLow();
        Drive_C_SetHigh();
        Drive_D_SetHigh();
        __delay_ms(speed);
        
        Drive_A_SetLow();   //0110
        Drive_B_SetHigh();
        Drive_C_SetHigh();
        Drive_D_SetLow();
        __delay_ms(speed);
        
        Drive_A_SetHigh();  //1100
        Drive_B_SetHigh();
        Drive_C_SetLow();
        Drive_D_SetLow();
        __delay_ms(speed);
        
        Drive_A_SetHigh();  //1001
        Drive_B_SetLow();
        Drive_C_SetLow();
        Drive_D_SetHigh();

    }
}


void executeCommand(char *command) {
    if (strcmp(command, "EnCat") == 0) {   // Enable Thermionic Cathode
        En_Cathode_SetHigh();
        printf("Thermionic Cathode Enabled.\r\n");
    }
    else if (strcmp(command, "EnIon") == 0) {   // Enable Ionizer Chips
        En_Ion_SetHigh();
        printf("Ionizers Enabled.\r\n");
    }
    else if (strcmp(command, "DisCat") == 0) {  // Disable Thermionic Cathode
        En_Cathode_SetLow();
        printf("Thermionic Cathode Disabled.\r\n");
    }
    else if (strcmp(command, "DisIon") == 0) {  // Disable Ionizer Chips
        En_Ion_SetLow();
        printf("Ionizers Disabled.\r\n");
    } 
    else if (strcmp(command, "EnBoth") == 0) {   // Enable both
        En_Pulse_SetHigh();
        En_Ion_SetHigh();
        En_Cathode_SetHigh();
        printf("Components Enabled.\r\n");
    }
    else if (strcmp(command, "DisBoth") == 0) {  // Disable both
        En_Pulse_SetLow();
        En_Ion_SetLow();
        En_Cathode_SetLow();
        printf("Components Disabled.\r\n");
    }
    else if (((atoi(command) >= -8192) && (atoi(command) <= 8192)) && (atoi(command) != 0)) {//Flow Valve Step Control
        steps = atoi(command);
        if(steps < 0){
            printf("Opening valve.\r\n");
            for(i=0; i>steps; i--) {
                full_drive(counter_clockwise);
            }
            printf("Done.\r\n");
        }
        else if(steps > 0) {
            printf("Closing valve.\r\n");
            for(i=0; i<steps; i++) {
                full_drive(clockwise);
            }
            printf("Done.\r\n");
        }
//        else if(steps == 0) {
//            printf("Incorrect command.\r\n");
//        }
    }
    else {
        printf("Incorrect command.\r\n");
    }
}

/*
                         Main application
 */

void main(void)
{
    // Initialize the device
    SYSTEM_Initialize();

    // If using interrupts in PIC18 High/Low Priority Mode you need to enable the Global High and Low Interrupts
    // If using interrupts in PIC Mid-Range Compatibility Mode you need to enable the Global and Peripheral Interrupts
    // Use the following macros to:

    // Enable the Global Interrupts

    // Disable the Global Interrupts
    //INTERRUPT_GlobalInterruptDisable();

    // Enable the Peripheral Interrupts

    // Disable the Peripheral Interrupts
    // INTERRUPT_PeripheralInterruptDisable();

//    if(!SPI1_Open(SPI1_DEFAULT)) {
//        printf("SPI not open.");
//        return;
//    }
//    SSP1CON1bits.SSPEN = 1; // Make sure SPI enabled
    
    printf("PIC RIOT Drive prototype interface.\r\n");
    printf("'EnCat/DisCat' to enable/disable Thermionic Cathode. \r\n");
    printf("'EnIon/DisIon' to enable/disable Ionizer. \r\n");
    printf("'EnBoth/DisBoth' to enable/disable both. \r\n");
    printf("Enter a positive value for clockwise turns of stepper motor. \r\n");
    printf("Enter a negative value for counter-clockwise turns of the stepper motor. \r\n");
    
    __delay_ms(50);
    //LDAC_SetLow();
    
    while (1) {
        // EUSART Code
        c = getch();
        data = c; // Converting to char
        if(data != '\n' && data != '\r')
        {
            command[index++] = data;
            if(index > MAX_CMD_LEN)
            {
                index = 0;
            }
        }
        
        if(data == '\n')
        {
            command[index] = '\0';
            index = 0;
            executeCommand(command);
        }
        
//        // ADC Code
//        ADC_result = 0;
//        ADCC_StartConversion(channel_ANC1);
//        while(!ADCC_IsConversionDone());
//        ADC_result = ADCC_GetConversionResult();
//        voltage = (ADC_result * 5.0)/1024; //Change multiplication for changing input voltage
        
    }
}



/**
 End of File
*/

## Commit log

2023-10-14 Add files via upload
    Altium Files for the power converter circuit
    [24V_to_3.3V_(for_MCU).SchDoc, 24_to_33V_(for_Ionizer_Chips).SchDoc, ECEN_403_Power_Circuit.PrjPcb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]
2023-10-14 Create circuits
2024-03-02 Create New-Power-Converter-Circuit
2024-03-02 Add files via upload
    Microcontroller Altium files for Alex to do stuff with.
    [ECEN 404 Schematic.PrjPcb, Microcontroller PCB 404.PcbDoc, Microcontroller Schematic 404.SchDoc]
